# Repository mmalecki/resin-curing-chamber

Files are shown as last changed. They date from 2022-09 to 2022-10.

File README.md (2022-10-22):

# Resin Curing Chamber
Parametrized DYI resin curing chamber, using UV LED strips.

Features:
  * simplicity - no moving parts and a short BOM of commodity electronics
  * fully customizable - build it as small, or as large as you wish, with the
    parts available to you
  * safe to operate - doesn't turn on unless the cover is closed, designed with
    protecting against light leaks in mind

| Front | Inside |
|:-----:|:---:|
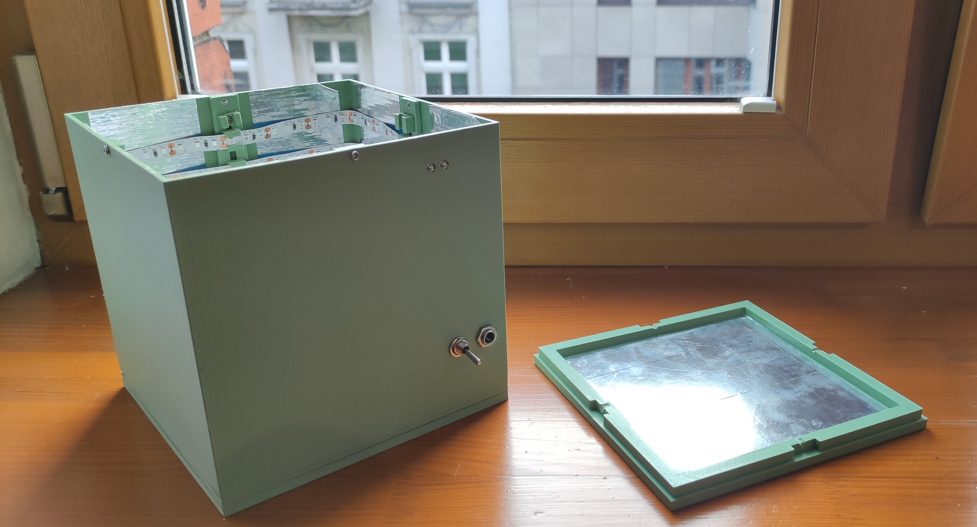
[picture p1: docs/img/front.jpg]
Front
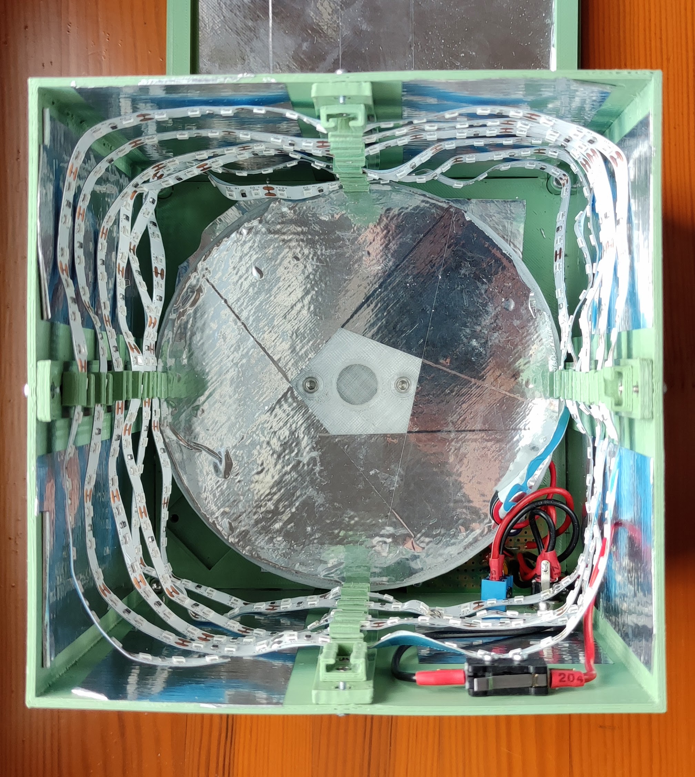
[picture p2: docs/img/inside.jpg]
Inside
|  |  |

## Build manual
See the [build manual document](./docs/build-manual.md) for BOM and instructions.

## Motivations
There is a bunch of DYI resin curing chamber projects out there, and with better
features. Why build another?

Initially I had intended for this project to have a turn-table based on a tiny
hobby DC motor with a reduction gearbox, therefore catching up on the feature set.

However, this was increasing the complexity a lot, causing me a lot of grief
as the engine I'd used was very underpowered, and, as I soon noticed, didn't have
much impact on the curing quality, probably due to the light source being all
around the part, and not in a single place, as in some other projects.

Additionally, the build volume of my printer is tiny, so I didn't really need
the size the other projects were offering out of the box. Instead, I wanted
something I could scale up while keeping the innards intact if I wanted to.

The goal for a next version is to revisit the turn-table concept, as well as add
in some form of a timer and display.

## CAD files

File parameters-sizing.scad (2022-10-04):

// All values are in millimeters.

// Main sizing parameters:
// Chamber height (maximum height of a fitting object):
chamber_h = 100;
// Bed diameter:
bed_d = 134;

// LED strip:
// The width of the LED strip you have:
led_strip_w = 8;
// And its thickness (measure at the thickest point, e.g. where the actual LED is):
led_strip_t = 1.6;

// Electronics PCB:
// Width (parallel to the base side):
pcb_w = 48;
// Length (extending towards the center):
pcb_l = 35;
// Maximum height of the components (with ample allowance):
pcb_h = 15;
// PCB thickness:
pcb_t = 1.75;
// PCB bolt spacing:
pcb_mount_bolt_s = 40.6;
// PCB bolt size:
pcb_mount_bolt = "M2";

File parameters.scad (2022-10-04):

use <catchnhole/catchnhole.scad>;
use <lookup-kv/lookup-kv.scad>;
use <next-bolt/next-bolt.scad>;
include <parameters-sizing.scad>;

$fn = 50;

// Standard fits.
tight_fit = 0.1;
fit = 0.25;
loose_fit = 0.5;

// The bolt we use by default.
bolt = "M3";
bolt_head_l = bolt_head_length(bolt, kind = "socket_head");

// Design rules:

// Minimal diameter of a standoff ended with a nut. The goal of this design rule
// is to provide adequate material around the nut.
nut_standoff_d = 8.8;

// Minimal height of a standoff ended with a nut. The goal of this design rule
// is to provide adequate material over the nut to provide holding power.
nut_standoff_h = nut_height(bolt) + 0.6;

// Minimal diameter of a bolt conduit standoff.
standoff_d = 7;

// Cover thickness:
cover_t = 2;
// How much side clearance the bed should have from cover:
cover_bed_clearance = 8;

// Arbirtrary height of the bed plater:
bed_h = 4.2;

// Arbirtrary height of the bed rim:
bed_rim_h = 2;
bed_rim_t = 2;

// Base:
// Arbirtrary height of the base plate:
base_h = 5;
// How recessed the mounted parts should be within the base:
base_mounting_inset = 2;
inset_base_h = base_h - base_mounting_inset;
assert(base_mounting_inset < base_h, "base mounting inset cannot be larger than base height");


// Calculated base edge:
base_d = bed_d + cover_bed_clearance + cover_t * 2;

// PCB mount:
pcb_mount_standoff_h = 7.5;
pcb_mount_w = pcb_mount_bolt_s + standoff_d;
pcb_mount_bolt_l = (base_h - base_mounting_inset) + pcb_mount_standoff_h + pcb_t;

bed_mount_d = 30;
bed_mount_h = pcb_h + pcb_mount_standoff_h;

// Arbirtrary spacing between the bolts connecting the bed and bed mount.
bed_mount_bed_bolt_s = 30;

bed_mount_bed_bolt = lookup_kv(next_bolt(bolt, bed_h + nut_standoff_h - bolt_head_l), "next");
bed_mount_bed_bolt_l = lookup_kv(bed_mount_bed_bolt, "length");
echo(str("BOM (bed-mount bed bolt): ", bolt, "x", bed_mount_bed_bolt_l));
bed_mount_bed_bolt_length_clearance = lookup_kv(bed_mount_bed_bolt, "length_clearance");
bed_mount_bed_bolt_standoff_h = nut_standoff_h + bed_mount_bed_bolt_length_clearance;

bed_mount_base_bolt = lookup_kv(next_bolt(bolt, bed_mount_h + inset_base_h - bolt_head_l), "previous");
bed_mount_base_bolt_l = lookup_kv(bed_mount_base_bolt, "length");
echo(str("BOM (bed-mount base bolt): ", bolt, "x", bed_mount_base_bolt_l));
bed_mount_base_bolt_countersink = lookup_kv(bed_mount_base_bolt, "countersink");

// How much distance is there between base top and beginning of the chamber
// (height of the under-bed machinery):
chamber_add_h = bed_mount_h + bed_h;

// The bolt we're using for mounting the LED mounts.
led_mount_bolt = "M2";

// The LED clamp is a U-shaped bracket with additional holders at the top.
led_mount_clamp_t = 1.2;
led_mount_clamp_h = 8;
// TODO: calculate this out of design rules (minimal bolt mating length) and LED mount bolt head length.
led_mount_clamp_back_t = 2;
led_mount_clamp_back_w = led_strip_w + fit;
led_mount_clamp_front_w = 0.625 * (led_mount_clamp_back_w + 2 * led_mount_clamp_t);
// TODO: next-bolt this
led_mount_clamp_bolt_l = 4;

// On the other side of the LED clamp is a rectangular pad that holds a nutcatch.
// It rightens itself as the bolt is tightened.
led_mount_pad_w = 8;
led_mount_pad_h = 6;
led_mount_pad_t = 2;

// LED mount rib (the vertical piece holding LED clamps):
led_mount_rib_w = 14;
led_mount_rib_t = 3;
// TODO: calculate the following 2 out of nut standoff ds
led_mount_rib_nutcatch_offset = 3;
led_mount_rib_channel_offset = 10;
// TODO: calculate this out of LED mount bolt d and clearance
led_mount_rib_channel_d = 2.5;
led_mount_rib_h = chamber_h + chamber_add_h;
led_mount_rib_bracket_l = 10;

// Floor:
floor_h = 5;
floor_bolt_inset = 2.5;

// Cover:
cover_fit = fit;
cover_base_offset = cover_t + cover_fit / 2;
cover_standoff_h = 10;
// Height of the cover:
cover_h = chamber_h + chamber_add_h;
cover_bolt_offset = (base_h - base_mounting_inset) + floor_h;

cover_bolt = lookup_kv(next_bolt(bolt, cover_standoff_h + cover_bolt_offset), "previous");
cover_bolt_l = lookup_kv(cover_bolt, "length");
cover_bolt_countersink = lookup_kv(cover_bolt, "countersink");

echo(str("BOM (cover bolt): ", bolt, "x", cover_bolt_l));

// Dimensions of the endstop:
endstop_bolt_spacing = 7;
endstop_bolt = "M2";
// When the endstop is activated, its total height (including the depressed lever) is this:
endstop_act_h = 11.9; 
// When the endstop is deactivated, its total height (including the returning lever) is this:
endstop_deact_h = 12.7;
endstop_pressed_h = 11.1;
endstop_h = 10.1;
endstop_l = 18.5;
endstop_w = 7.3;
endstop_bolt_offset = 2.1;

endstop_cover_offset_add = 4;
endstop_cover_offset = cover_h + endstop_bolt_offset - endstop_deact_h - endstop_cover_offset_add;
endstop_activator_h = (endstop_deact_h - endstop_pressed_h) * 3/4 + endstop_cover_offset_add;

cover_dc_input_d = 7.6 + fit;
cover_switch_d = 5.85 + fit;
cover_dc_input_bottom_offset = pcb_mount_standoff_h + 25;
cover_dc_input_side_offset = cover_dc_input_d / 2 + cover_t + standoff_d;
cover_switch_side_offset = cover_dc_input_side_offset + cover_dc_input_d + cover_dc_input_d;
cover_led_mount_bolt_clearance = 0.2;

cover_top_h = 5;

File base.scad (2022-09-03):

use <catchnhole/catchnhole.scad>;
use <bed.scad>;
use <bed-mount.scad>;
use <cover.scad>;
use <led-mount.scad>;
use <pcb-mount.scad>;
include <parameters.scad>;

module base_led_mount () {
  translate([
    base_d / 2 - cover_base_offset,
    led_mount_rib_w / 2,
    0
  ]) {
    rotate([0, 0, 180]) {
      translate([0, 0, base_h - base_mounting_inset])
        translate([-fit / 2, -fit / 2])
          cube([led_mount_rib_bracket_l + fit, led_mount_rib_w + fit, base_mounting_inset]);

      translate([
        (led_mount_rib_t + led_mount_rib_bracket_l) / 2,
        led_mount_rib_w / 2,
      ]) {
        led_mount_rib_bolts();
        led_mount_rib_mounts() nutcatch_parallel(led_mount_bolt);
      }
    }
  }
}

module base () {
  difference () {
    union () {
      cube([base_d, base_d, base_h - base_mounting_inset]);
      translate([cover_t + cover_fit / 2, cover_t + cover_fit / 2, base_mounting_inset]) {
        d = base_d - 2 * cover_t - fit;
        cube([d, d, base_h - base_mounting_inset]);
      }
    }


    translate([base_d / 2, base_d / 2]) {
      bed_mount_base_bolts();
      bed_mount_base_mounts() nutcatch_parallel(bolt);

      translate([-bed_mount_d / 2  -fit / 2, -bed_mount_d / 2-fit / 2, base_h - base_mounting_inset]) {
        cube([bed_mount_d + fit, bed_mount_d + fit, base_mounting_inset]);
      }

      base_led_mount();
      rotate([0, 0, 90]) base_led_mount();
      rotate([0, 0, 180]) base_led_mount();
      rotate([0, 0, 270]) base_led_mount();

      translate([0, 0, floor_h]) cover_bolts();
      translate([0, 0, base_h - base_mounting_inset])
        cover_mounts() cylinder(d = standoff_d + fit, h = base_mounting_inset);
    }

    translate([
      cover_base_offset + standoff_d,
      base_d - cover_base_offset - standoff_d - fit,
    ]) {
      translate([0, 0, base_h - base_mounting_inset])
        cube([pcb_mount_w + fit, standoff_d + fit, base_mounting_inset]);

      translate([pcb_mount_w / 2 + fit / 2, standoff_d / 2 - fit / 2]) {
        pcb_mount_mounts() nutcatch_parallel(pcb_mount_bolt);
        pcb_mount_bolts();
      }
    }
  }

}

base();

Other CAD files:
bed-mount.scad
bed.scad
cover-top.scad
cover.scad
floor.scad
led-mount-clamp.scad
led-mount-pad.scad
led-mount.scad
mockup.scad
pcb-mount.scad

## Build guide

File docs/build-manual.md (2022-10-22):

# Build manual

## What you need

This is as hand-wavy as it gets, because nearly every single part of this
project is configurable to fit whatever parts you have on hand, and the quantities
of some parts depend on the build size.
Unless you've changed some internal parameters (in `parameters.scad` instead
of `parameters-sizing.scad`), the bolt lengths should stay the same.

| **Item** | **Quantity** |
|:---|---:|
| UV LED strip | As desired |
| Reflective tape | As needed |
| DC power supply (compatible with the UV LED strip) | 1 |
| Panel mount DC power jack | 1 |
| Panel mount toggle switch | 1 |
| Prototyping PCB | 1 |
| Mechanical endstop switch | 1 |
| Heat shrink sleeve | As needed |
| M3 nuts | 12 |
| M2 nuts | 10 + as needed |
| M3x6 bolt | 2 |
| M3x16 bolt | 4 |
| M3x22 bolt | 4 |
| **Printed parts** | |
| Base | 1 |
| Bed | 1 |
| Bed mount | 1 |
| Cover | 1 |
| Cover top | 1 |
| Floor | 1 |
| PCB mount | 1 |
| LED mount | 4 |
| LED mount clamp & pad | As needed |

## Configuring the build
First, you need pick the sizing parameters for your build: chamber height and
bed diameter, as well as LED strip width and thickness.
Open [`parameters-sizing.scad`](../parameters-sizing.scad) and edit the relevant variables.

## Building the STLs
After you've edited `parameters-sizing.scad`, you can build the STL files by running
`./scripts/build`. This will create STL files in the `output` directory.

If you've changed any internal parameters, here's where to look for new bolt
lengths. These will be output by OpenSCAD, albeit repeated a couple times as
the output renders.

## Printing
* **Material**: Any material for everything but the cover and LED mount parts.
  Use PETG for those - the chamber may get toasty inside.
* **Layer height**: At most 0.2 mm layer height (recommend using [variable layer height](https://help.prusa3d.com/article/variable-layer-height-function_1750)
  with adaptive layer height, which will use different layer height for the
  base and the hinges).
* **Infill**: 15%
* **Perimeters**: 3

## Putting it together

### Electronics
You'll need to connect the toggle switch and the mechanical endstop switch
in series with the LED strip.

### Case
1. Insert the 4 M3 nuts into the nutcaches in the bottom of the floor.
2. Insert the 10 M2 and 4 M3 nuts into the nutcatches in the base.
3. Mount the PCB on the PCB mount, to the base. Leave the switches and LED strip
unmounted for the time being.
4. Mount the LED mounts to the base.
5. Insert the 2 M3 nuts into the nutcatches in the bed mount.
6. Mount the bed mount to the base. Don't mount the bed yet, it's going to get
in the way of mounting the LED strips.
7. Insert nuts into nutcatches on the LED clamp pads. Insert the pads into the 
channel on the back of the LED mount, and the clamps on the front. Join them
together through the hole in the LED mount with a M2 bolt. As you tighten the
bolt, the pad should rotate in place.
8. Start wrapping the LED strip around the chamber by inserting the strip into
the clamps.
9. Mount the cover with the 4 M3 bolts, mount the toggle swich (through panel)
and endstop (with M2 bolts) to it.
10. Put the cover top on top, and you're done.

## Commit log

2022-07-19 Start designing the bed
    [bed.scad, mockup.scad, parameters.scad]
2022-07-19 Move the gear, add a "nip" to avoid mating the entire bed gear with the base
    [bed.scad, mockup.scad, parameters.scad]
2022-07-24 More or less finish the base
    [bed.scad, mockup.scad, parameters.scad]
2022-07-24 Refactor and document `parameters.scad`
    [parameters.scad]
2022-07-24 Add some more comments to `parameters.scad`
    [parameters.scad]
2022-07-24 Add the base
    [frame.scad]
2022-07-24 Increase shaft bolt head dia clearance
    [bed.scad, frame.scad, parameters.scad]
2022-07-24 `frame.scad` -> `base.scad`
    [base.scad, mockup.scad]
2022-07-24 Extract out the mount point placing of engine mount and bed raiser
    [base.scad]
2022-07-25 Move the bearing into the bed
    [base.scad, bed.scad, mockup.scad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]
2022-07-25 Use the `bed_axle` for differences throughout
    Move it to `bed.scad`.
    [base.scad, bed.scad]
2022-07-26 Start working on cover and LED mounts
    [base.scad, bed.scad, led-mount.scad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]
2022-07-26 Implement LED mouting
    [base.scad, bed.scad, led-mount.scad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]
2022-07-26 Create nutcatches for the LED mounts
    [base.scad]
2022-07-27 Add a PCB mount and a cover
    Do not set a special inset for the cover.
    [base.scad, mockup.scad, parameters.scad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]
2022-07-28 DRY the LED mount
    [led-mount.scad]
2022-07-29 Add head clearance to the bed axle bolt
    [bed.scad]
2022-07-30 Add a floor
    [floor.scad, parameters.scad]
2022-07-30 Add a LED mount nutcatch offset parameter
    [parameters.scad]
2022-07-30 Add the floor to mockup
    [mockup.scad]
2022-07-30 Include the bed and gear heights in `chamber_add_h`
    [parameters.scad]
2022-07-30 Add beginnings of a cover
    [cover.scad]
2022-08-06 Add a cover, add cover passthroughs
    Add a cover top.
    [base.scad, bed-raiser.scad, cover-top.scad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]
2022-08-06 Make displaying the LED mount rib optional
    [mockup.scad]
2022-08-15 Add the v1 bed - bed raiser mount shim
    [bed-as-bed-raiser-mount.scad, bed.scad, parameters.scad]
2022-09-03 Remove any and all mentions of a rotary table
    [base.scad, bed-as-bed-raiser-mount.scad, bed-mount.scad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]
2022-09-03 Fix mockup z offsets
    [mockup.scad]
2022-09-03 Change the coordinate system around bed mount
    Make it centric instead.
    [base.scad, bed-mount.scad]
2022-09-03 Fix `chamber_add_h` calculation
    The cover starts at the same point the bed mount does, so the inset
    doesn't matter.
    [parameters.scad]
2022-09-03 Move the bed bolt spacing where it belongs
    [bed.scad, parameters.scad]
2022-10-03 Remove unused `press_fit`
    [parameters.scad]
2022-10-03 Fix floor bed mount screw run-out hole positioning
    [floor.scad]
2022-10-03 Remove superfluous variables around LED mounts, add some commends
    [led-mount.scad, parameters.scad]
2022-10-03 Make more notes re arbirtrary parameters
    [parameters.scad]
2022-10-04 Extract main sizing parameters
    [parameters-sizing.scad, parameters.scad]
2022-10-04 Break out the LED mount clamp and pad
    [led-mount-clamp.scad, led-mount-pad.scad, led-mount.scad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]
2022-10-04 Move PCB parameters to sizing, add notes to others
    [parameters-sizing.scad, parameters.scad]
2022-10-04 Fix mockup LED mount clamp & pad positioning
    [mockup.scad]
